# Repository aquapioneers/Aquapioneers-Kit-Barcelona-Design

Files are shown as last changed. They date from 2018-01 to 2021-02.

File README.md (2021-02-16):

# The Aquapioneers Kit Barcelona Design

The Aquapioneers kit can transform a 54L (60x30x30 cm) aquarium into an aquaponic ecosystem. At the intersection of hardware and ecology, the ecosystem will allow you to grow fresh and tasty food all year round. This little piece of nature, will engage and inspire you, your family and your friends.

What makes the Aquapioneers kit different from other aquaponics kits, is its open source design, which was designed so that anyone can download and manufacture the kit locally in any digital manufacturing workshop, maker space or fab lab.

aquapioneers kit

## CNC milling design files

- Version 1 for a 50L Aquarium could be download [here](https://github.com/aquapioneers/Aquapioneers-Kit-Barcelona-Design/tree/master/CAD%20Files/Version%201%20for%2050L%20Aquarium) 
- Version 2 for a 50L Aquarium could be download [here](https://github.com/aquapioneers/Aquapioneers-Kit-Barcelona-Design/tree/master/CAD%20Files/Version%202%20for%2050%20L%20Aquarium) 
- Version 2 for a 180L Aquarium could be download [here](https://github.com/aquapioneers/Aquapioneers-Kit-Barcelona-Design/tree/master/CAD%20Files/Version%202%20for%20180%20L%20Aquarium) 

## Aquapioneers Ecosystem anatomy

anatomy 1

## Project main documentation

The user manual has been divided into four blocks following the Aquapioneers Ecosystem anatomy to ease its construction, assembly and use.

anatomy 2

The release of this documentation is progressive, meaning that the so far “The Body”, "The Blood", "The Nervous System" and "The Life" parts have been published. These editions will be regularly updated as a whole to reflect the comments and questions of our community. 

## Video tutorials

aquapioneers kit

Last but not the least, we have created a [Youtube channel ](https://www.youtube.com/playlist?list=PLUFhb7gQAOXpYl2u4EjiyPYbu-uKQxlLc) where we post some video tutorials to help you out related to the FAQs when it comes to maintain the ecosystem

## Contributions & Community forum

We are constantly working on improving the documentation but still we encourage you to Fork the project and do a Pull request with your contributions. We thus encourage you warmly to leave any comments / suggestions / questions on our [forum](http://aquapioneers.io/community-forum/) to be part of our community-based continuous improvement!

## Open Source Non Commercial License - Why ?

All the hardware design files is released under creative license [CC-BY-NC 4.0](https://creativecommons.org/licenses/by-nc/4.0/).Thi  license gives anyone the right to download, edit and remix their own versions of the AQUAPIONEERS ECOSYSTEM designs. We think participation in design is something to be actively encouraged. By adapting, improving and creating new variations of the ecosystem we hope to encourage research, innovation and a spirit of collaboration.

Because empowering people is one of the fundamental pillars of our project, we believe that everybody should have free access to this documentation to explore aquaponics and digital fabrication. Unfortunately in 2017 it is not yet possible to make a living out of free work.. this is why we have decided to limit the free use of our work to individuals. While we hope to inspire sustainable innovation with our work, we believe that economic value created from inventions should also benefit the inventors. This is why commercial use of this documentation will only be permitted through formal collaboration agreements. If you are interested in making commercial use of this work, please get in touch with us at info@aquapioneers.io and we’ll do our best to find a way to work together!

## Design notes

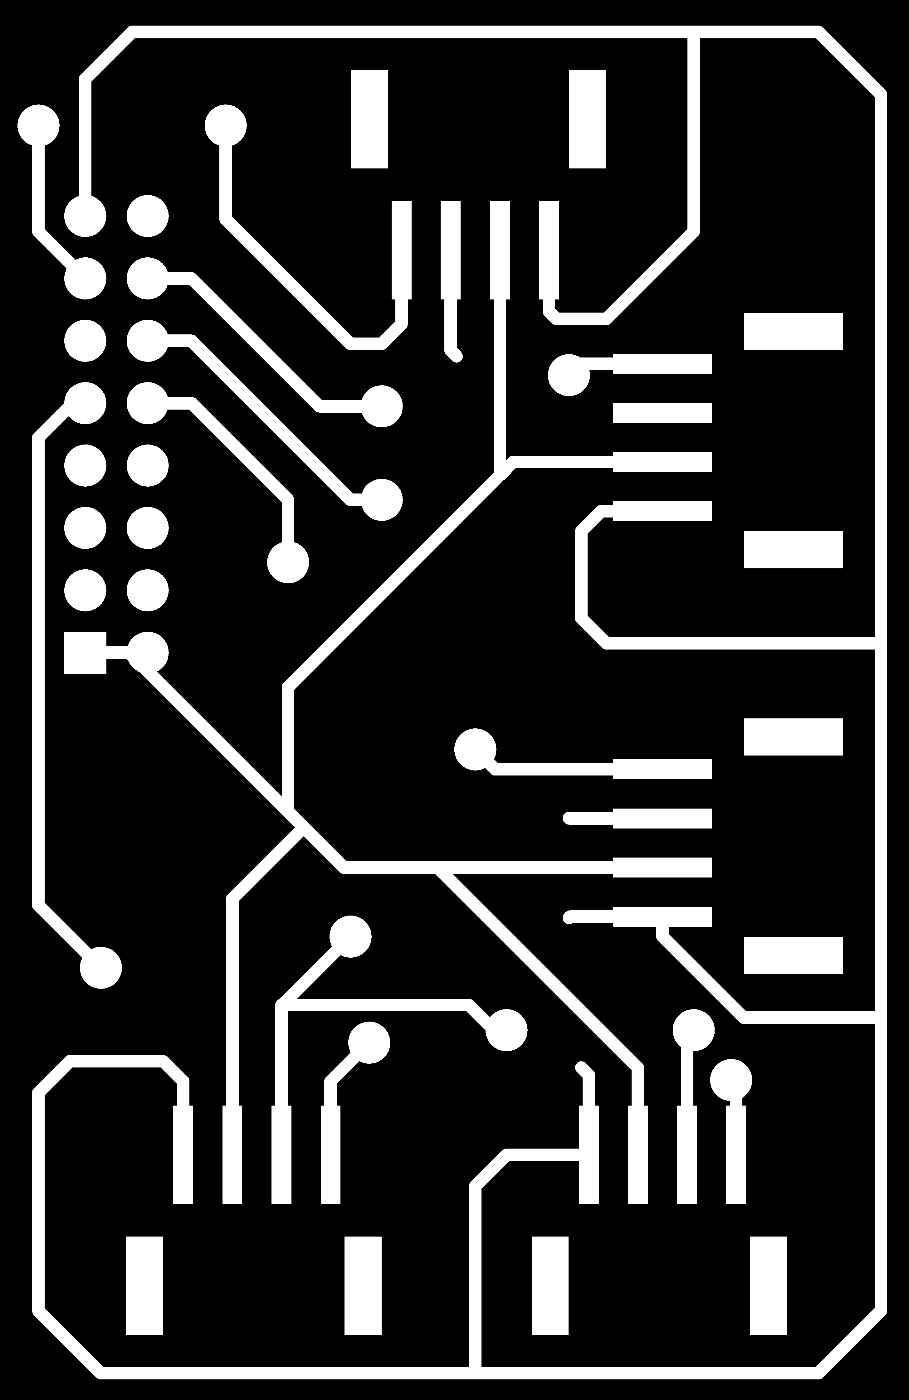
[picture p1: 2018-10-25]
Monitoring-kit-hardware/PCB layout/Aquapioneers PCB -Traces - Front.Cu.png

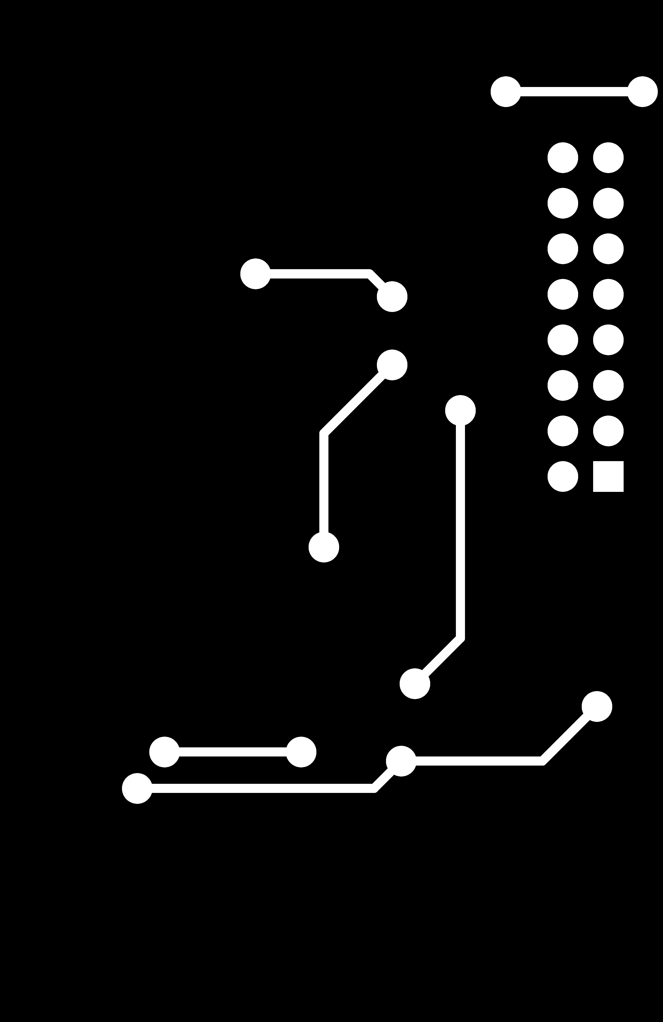
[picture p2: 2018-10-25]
Monitoring-kit-hardware/PCB layout/Aquapioneers PCB -Traces - Back.Cu.png

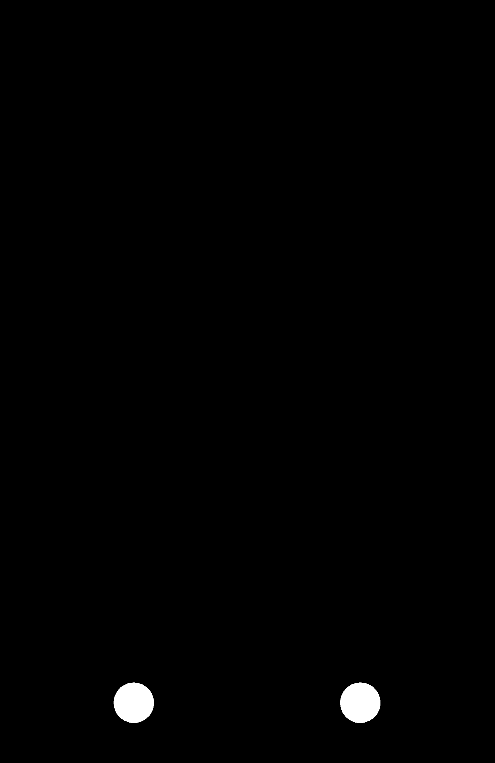
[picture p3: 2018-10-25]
Monitoring-kit-hardware/PCB layout/Aquapioneers PCB -Pins - Front.Cu.png

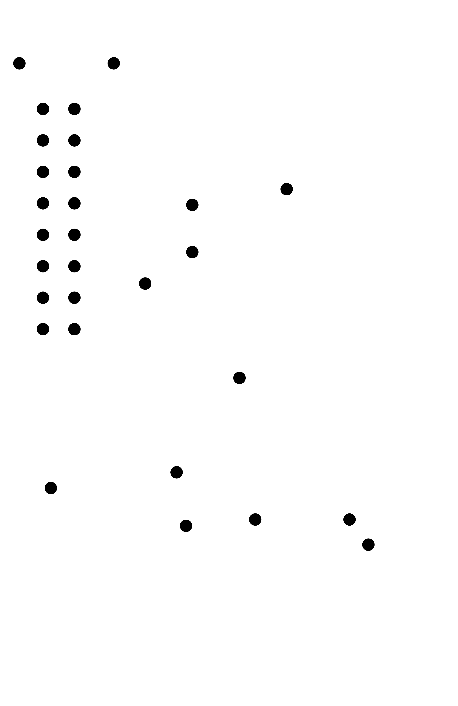
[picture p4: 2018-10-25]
Monitoring-kit-hardware/PCB layout/Aquapioneers PCB - Edge Cuts - Front.Cu.png

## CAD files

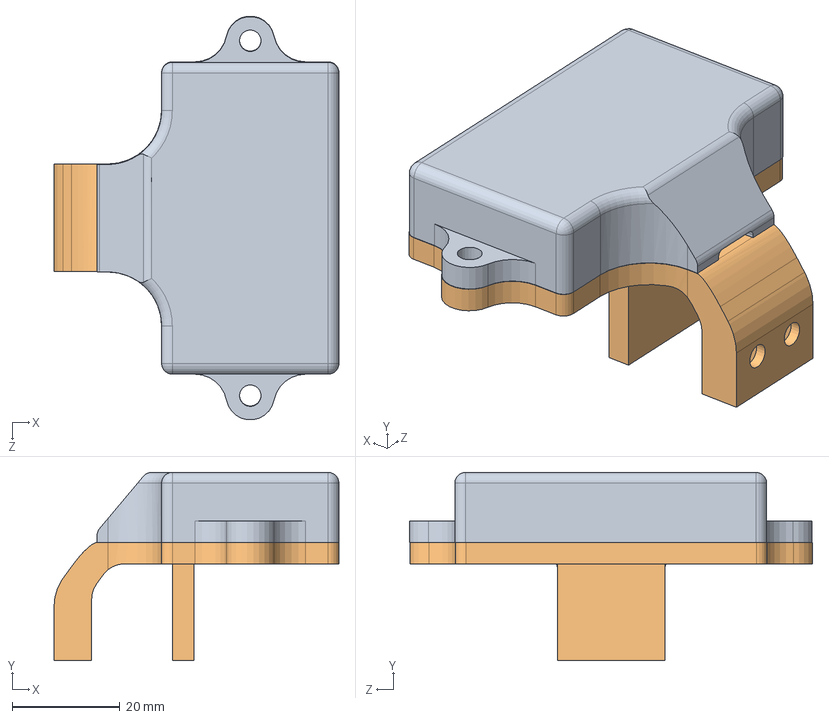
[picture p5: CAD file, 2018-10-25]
Monitoring-kit-hardware/3D printed ultrasonic sensor case/Assembly.SLDASM
53.0 x 35.0 x 75.0 mm
Top
Bottom
Ultrasonic_Ranger grove

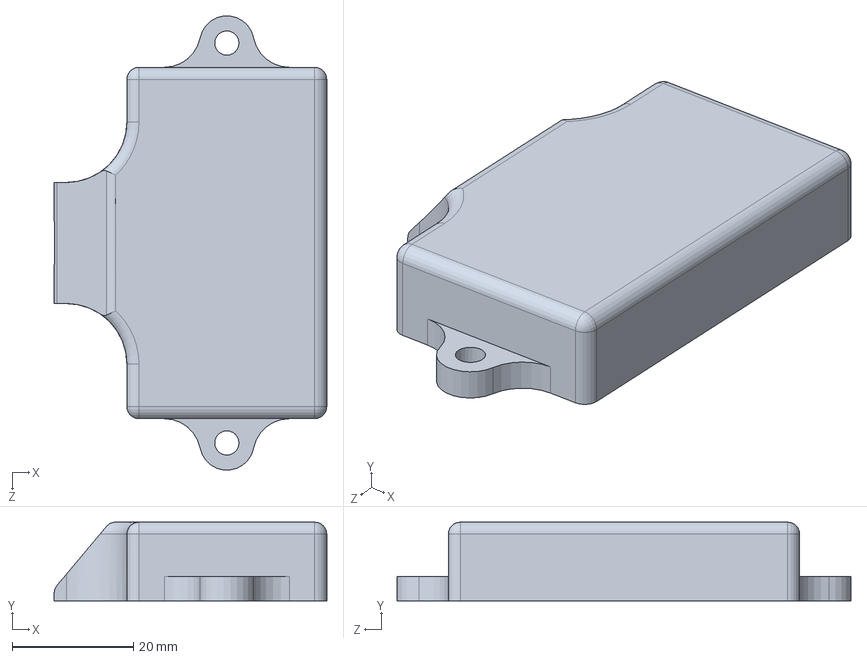
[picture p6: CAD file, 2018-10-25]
Monitoring-kit-hardware/3D printed ultrasonic sensor case/Top.SLDPRT
45.0 x 13.0 x 74.9 mm

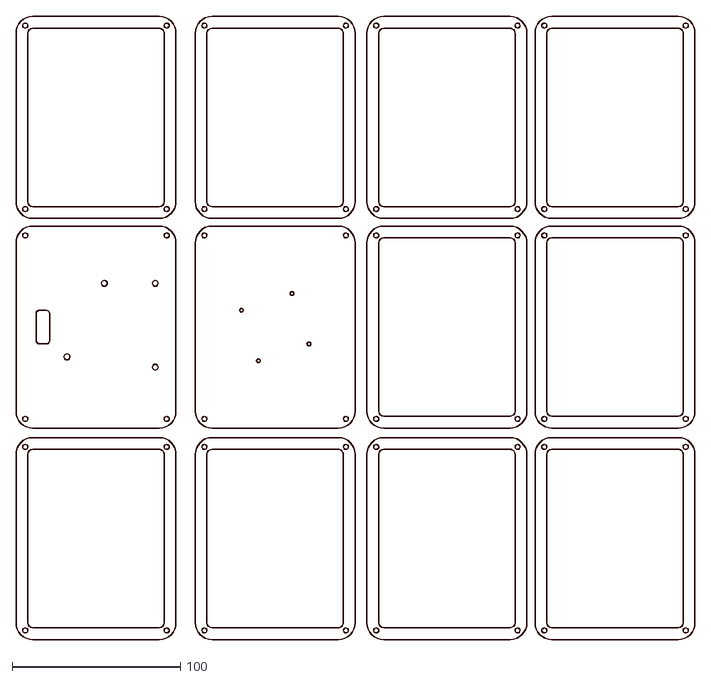
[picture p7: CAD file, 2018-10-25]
Monitoring-kit-hardware/Board case/Nesting Board Case.dxf
403.3 x 370.2

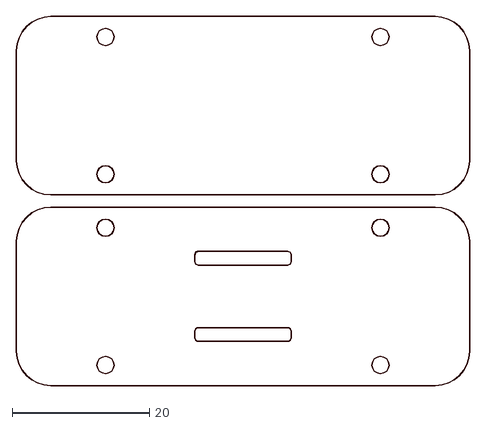
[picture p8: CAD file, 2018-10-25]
Monitoring-kit-hardware/SHT-31 and Light sensor/Nesting SHT-31 and Light sensor.DXF
66.0 x 53.8

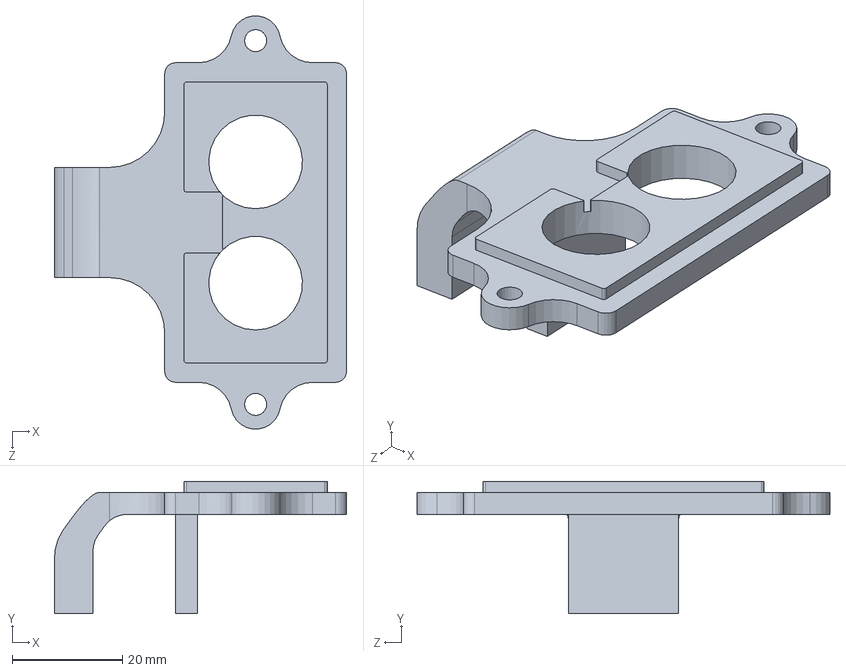
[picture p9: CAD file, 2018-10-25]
Monitoring-kit-hardware/3D printed ultrasonic sensor case/Bottom.SLDPRT
53.0 x 24.0 x 74.9 mm

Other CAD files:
CAD Files/Version 1 for 50L Aquarium/Aquapioneers_Kit_v1.6_18mm_Nesting-2.dwg
CAD Files/Version 2 for 180 L Aquarium/Aquapioneers_Kit_v2_18mm_180L_Nesting.DWG
CAD Files/Version 2 for 50 L Aquarium/Aquapioneers_Kit_v2_18mm_Nesting.dwg
CAD Files/Version 2 for 50 L Aquarium/Aquapioneers_Kit_v2_18mm_3D.dwg
CAD Files/Version 1 for 50L Aquarium/Aquapioneers_Kit_v1.6_18mm_Nesting-2.3dm
CAD Files/Version 2 for 180 L Aquarium/Aquapioneers_Kit_v2_18mm_180L_Nesting.3dm
CAD Files/Version 2 for 50 L Aquarium/Aquapioneers_Kit_v2_18mm_Nesting.3dm
Monitoring-kit-hardware/3D printed ultrasonic sensor case/Bottom.STL
Monitoring-kit-hardware/3D printed ultrasonic sensor case/Top.STL
Monitoring-kit-hardware/Board case/Rhino Nesting Board Case.3dm
Monitoring-kit-hardware/SHT-31 and Light sensor/Nesting SHT-31 and Light sensor.3dm

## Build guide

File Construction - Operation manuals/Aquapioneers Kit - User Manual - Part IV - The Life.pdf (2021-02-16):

# Download kit

### Free documentation & blueprints for Aquapioneers Kit Part IV - Biological System - The Life

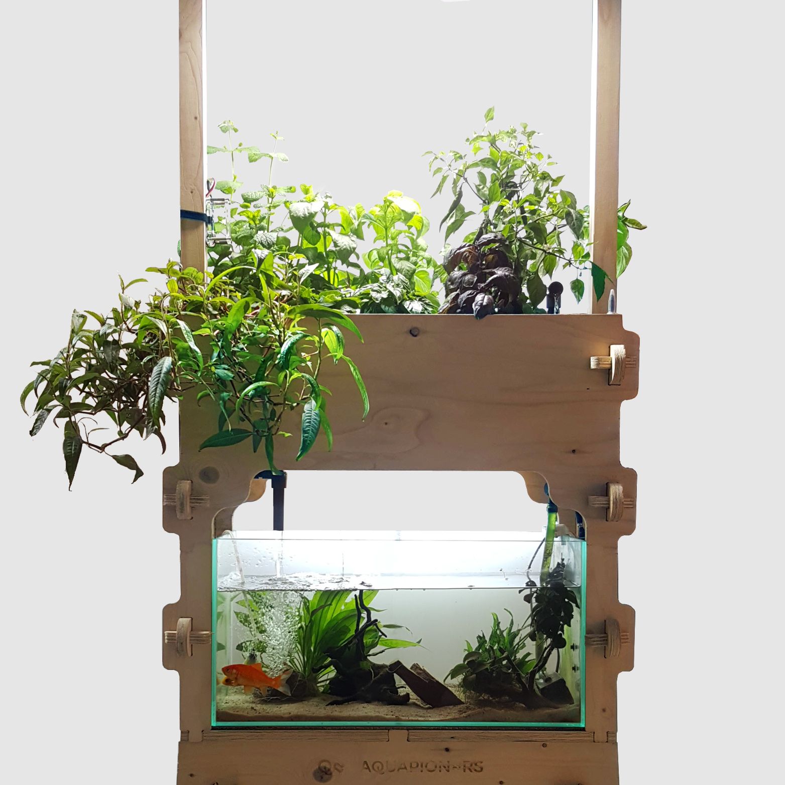
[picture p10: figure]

1. Almost ready to have your fresh aromatics all year round ! | 3
2. Starting up (cycling) your ecosystem | 4
2.1 Bill of materials | 4
2.2 Start the water irrigation system | 5
2.3 Start cycling your ecosystem | 8
3. Troubleshooting | 10
3.1 The bell siphon | 10
3.2 The water inlet | 12
4. Some species of fish that can inhabit your ecosystem | 15
5. Some herbs and leafy greens you can grow | 15
6. How to care for your kit | 16
6.1 Daily tasks | 16
6.2 Weekly tasks | 18
6.3 Ranges for water quality parameters | 21
Annex I : Aquaponic design ratios | 23
Annex II: Interesting Aquaponics links | 24

# 1. Almost ready to have your fresh aromatics all year round !

In less than two months, your Aquapioneers Kit could look likes something like the picture below. However there are some crucials biological steps to put in place before your aquaponics jungle takes place. In this section we will explain you how to kickstart the biological ecosystem and how to take car of it in order to grow with confidence.

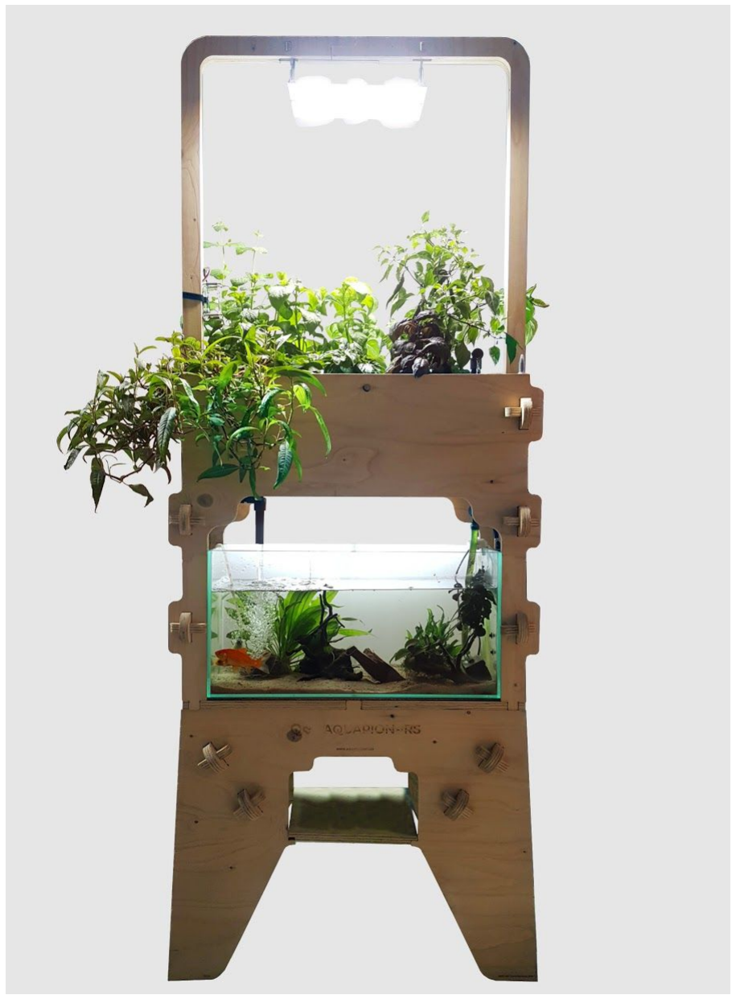
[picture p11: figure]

# 2. Starting up (cycling) your ecosystem

An aquaponic system needs about a month to establish a biological equilibrium between plants, fish and bacteria. This is due to the fact that the bacteria which filter the fish waste grow very slowly on the filter material we put at their disposal. While these nitrifying bacteria are ubiquitous and do not need to be artificially introduced into the system, it is fundamental to introduce a source of ammonia (NH4), simulating fish waste, which they can “train” to decompose into the nitrate (NO3) fertilizer we are after. We should not introduce fish until the filter is properly established, since these might die by self-intoxication. The safest way to do this is to add controlled dosages of ammonium chloride, a cheap and harmless chemical available. Nitrite concentrations should be monitored. Over time, ammonia (NH4) will be degraded first into nitrite (NO2) and finally into nitrate (NO3), so that globally, if you measure all three components over time, you should get a graph similar to the something below:

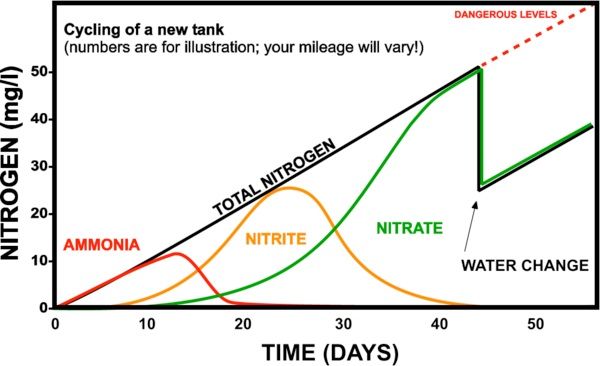
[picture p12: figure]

## 2.1 Bill of materials

For this you will need the following:

35 L of PH 7
clay pebble

Ammonium chloride
(AC) powder

NH4
water test

NO3
water test

NO2
water test
Price: 10-15€ | Price: 1€ | Price: 10€ | Price: 10€ | Price: 10€

## 2.2 Start the water irrigation system

1

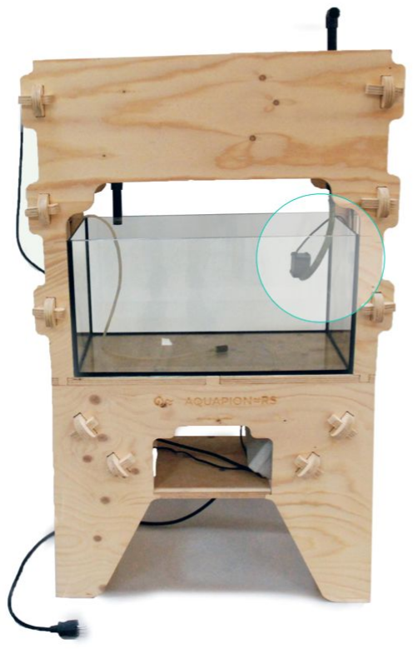
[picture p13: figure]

The entire electrical system is now in place, but “Do not plug your system to the mains power” until there is water in the fish tank, as this will run your water pump dry and possibly destroy it. To facilitate adding water to the aquarium you will remove the growbed for a while. To do so, first disconnect the flexible pipe to the water pump connector and the 12 Volts LED strip connector as well.
2

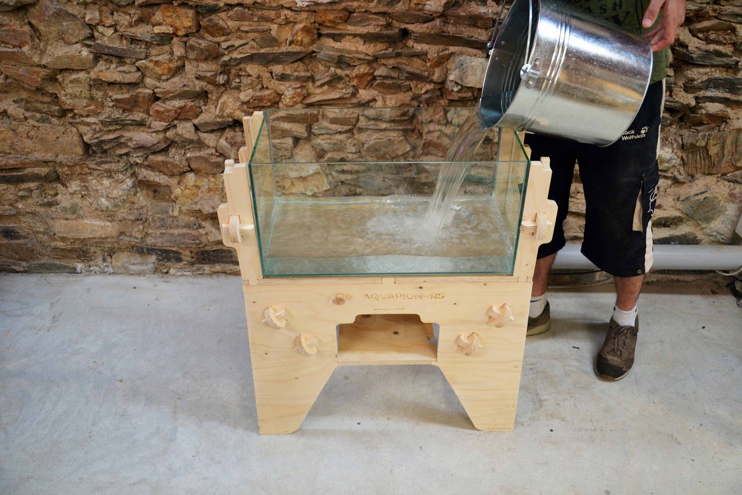
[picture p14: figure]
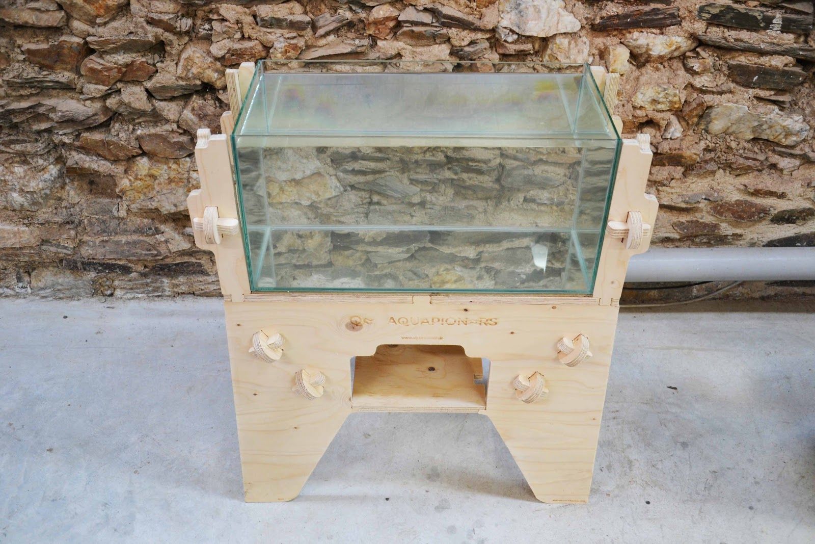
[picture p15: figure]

You will be able then to fill the aquarium. Tap water is OK.

3

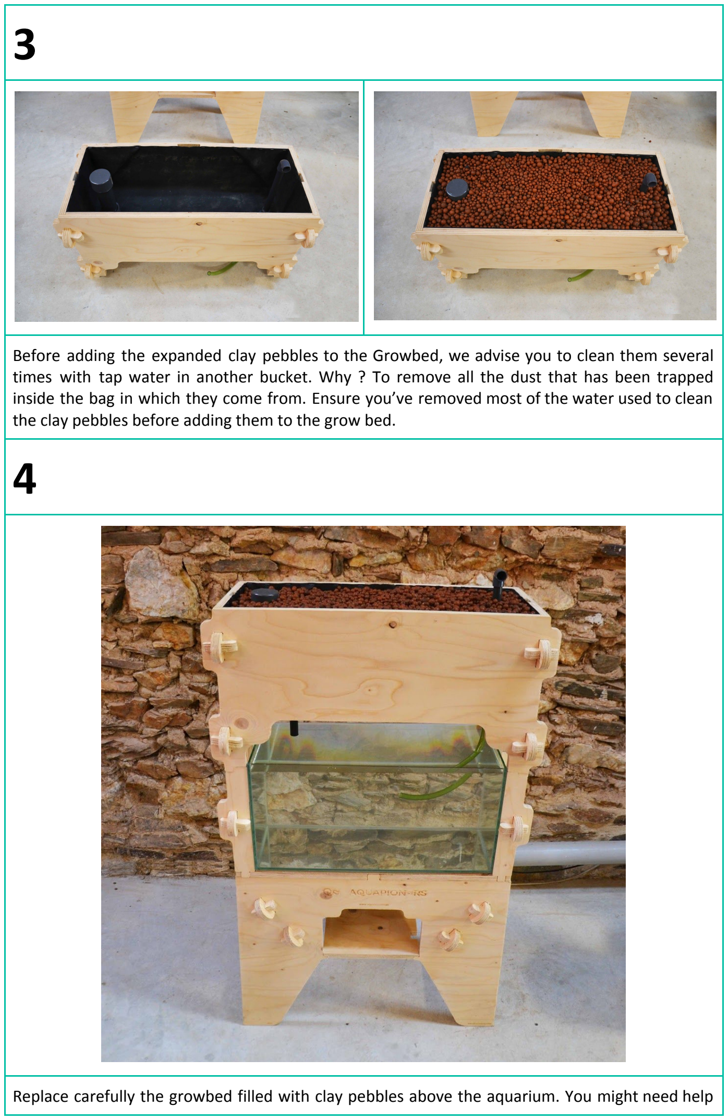
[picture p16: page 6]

Before adding the expanded clay pebbles to the Growbed, we advise you to clean them several times with tap water in another bucket. Why ? To remove all the dust that has been trapped inside the bag in which they come from. Ensure you’ve removed most of the water used to clean the clay pebbles before adding them to the grow bed.
4

Replace carefully the growbed filled with clay pebbles above the aquarium. You might need help from a peer since it could be quite heavy.
5

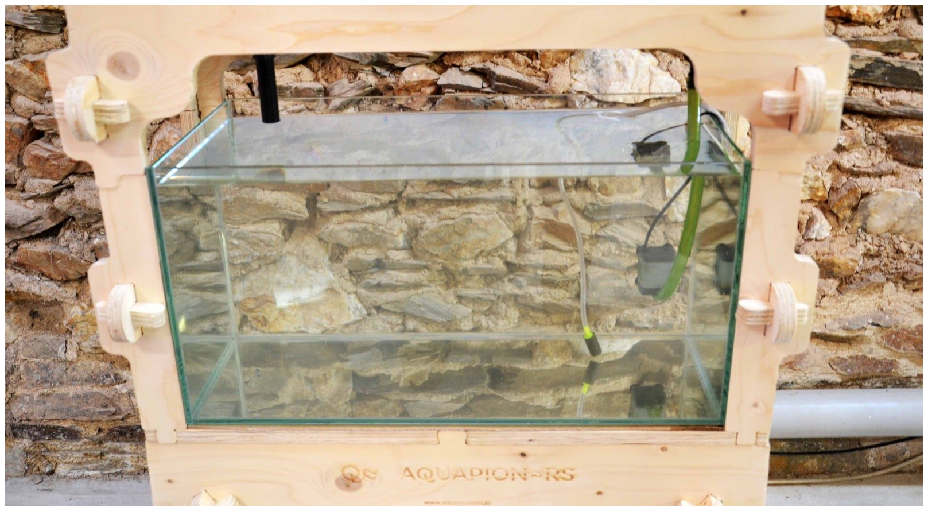
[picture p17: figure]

Replace the water pump inside the aquarium by reconnecting it to the green flexible pipe. Add the air pump tube in the aquarium as well.
6

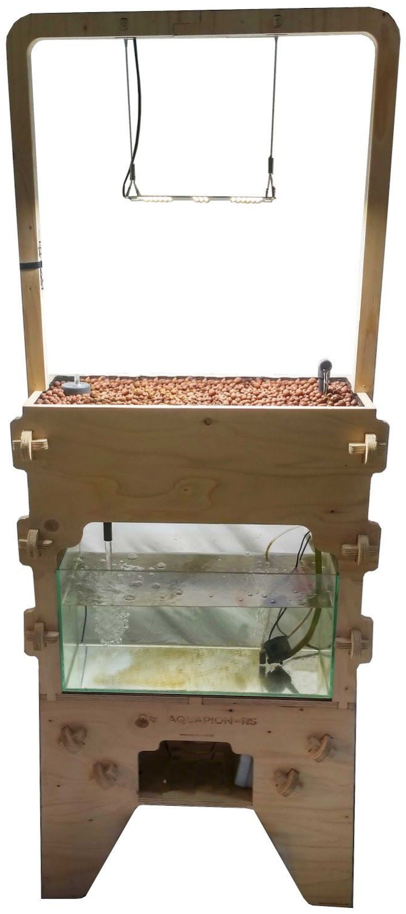
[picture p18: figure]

Last but no the least, you can add the lighting structure on top of growbed. However, please note that till your ecosystem is not cycled and planted you will not need to use the growing light. Before connecting your system to the main power, just make sure your electrical box is sealed. Then here you go !

## 2.3 Start cycling your ecosystem

1

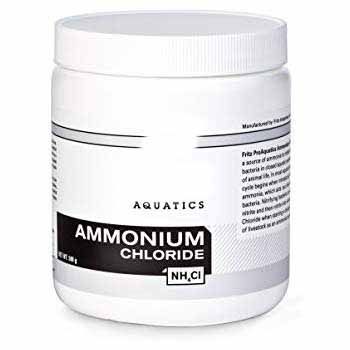
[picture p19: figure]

With an Aquapioneers kit of 50 L, we recommend to introduce ammonium chloride (AC) powder and test for ammonia, nitrite and nitrate with the help of the table on the following page (we recommend to print it and put it next to the kit to ease the follow up). An “X” marks the days in which we recommend to carry out the corresponding water test. The number in the column “AC dosis (g)” corresponds to the amount of ammonium chloride chemical to introduce into your system on that day. This dosage increases over time as the bacteria community grows stronger and is able to process more waste, until it matches the amount of ammonia produced daily by the amount of fish we’d like to introduce into our system.
2

IMPORTANT: If you want to use this table on a system with different size and amount of fish, you will need to adapt the dosages you introduce to your system. Do do this, IF you follow the design principles in Annex II, just divide the number in column 3 by 50, and then multiply by the amount of liters in your system. For example, if your system has 600 liters as in the example in section 2, the first dosis of ammonium chloride you need to introduce will be 0.2 g / 50 liters * 600 liters = 2.4 grams of ammonium chloride (AC).

Notes:
- The test should be carried out before introducing a new ammonium chloride dosis.
- The kit is properly cycled (and safe for fish) once nitrite (NO2) levels remain below 0,15 mg / Lt after minimum 2 weeks of cycling.

## Guide to start the nitrogen cycle for the Aquapioneers kit

Day | Date | AC dosis (g) | NO2 test | Value | NO3 test | Value
1 | | 0.2 | X | | X

2

3

4

5

6

7 | | 0.2 | X | | X

8

9

10

11 | | 0.2 | X | | X

12

13

14

15

16

17

18 | | 0.4 | X | | X

19

20

21

22

23

24 | | 0.6 | X | | X

25

26

27

28

29

30 | | 0.8 | X | | X

31

32

33 | | 0.8

34

35

36 | | 1.2 | X | | X

37

38

39 | | 1.2

40

41 | | | X | | X

# 3. Troubleshooting

Once your system is running, you might “or not” encounter some mechanical or electrical issues. You will find the most common ones below with our troubleshooting approach.

## 3.1 The bell siphon

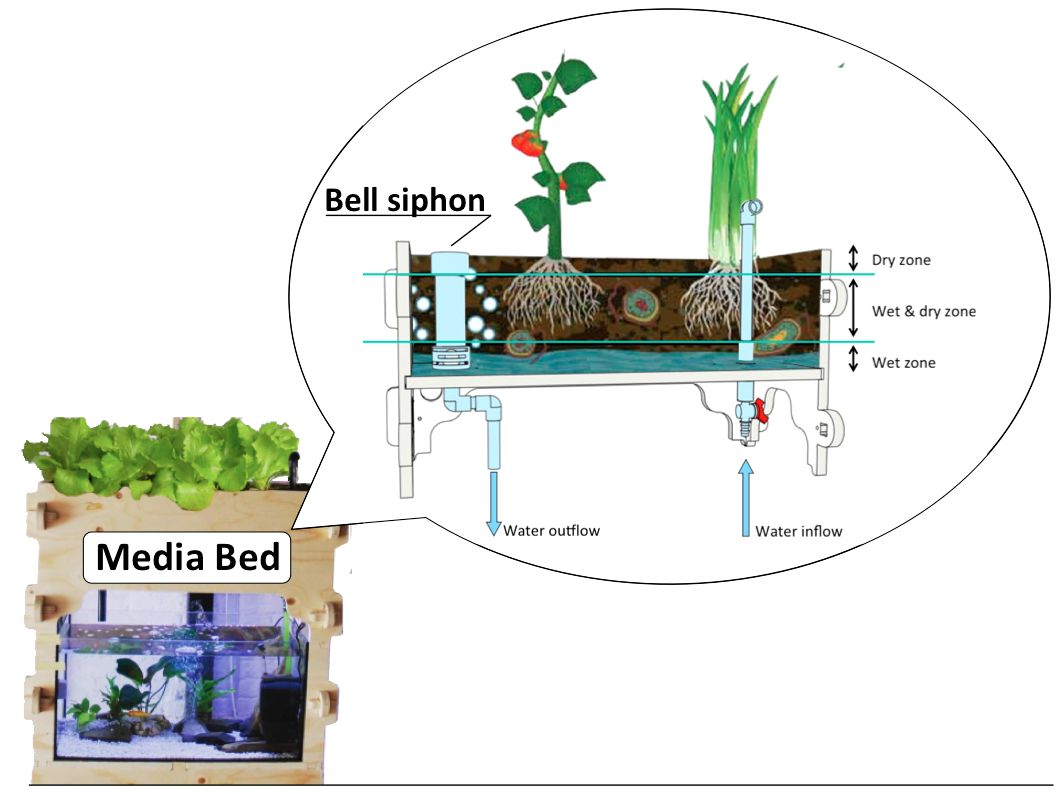
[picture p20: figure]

Media Bed technique that is used in the Aquapioneers kit, works with a Bell siphon which is a type of autosiphon that exploits a few physical laws of hydrodynamics and allows the media bed to flood and drain automatically, periodically, without a timer. This alternation ensures both high humidity and high oxygen levels in the Media Bed - exactly what your plant roots and nitrifying bacteria need! There is one downside to the bell siphon: Its proper function depends on the water flow of your pump. A correctly operating bell siphon drains the entire media bed water in less than a minute, then completely stops flowing until the media bed is full of water again, and the cycle starts anew.

If the water flow from the siphon is low (+/- the flow of the water inlet) and the water level remains constant, your Bell Siphon is not working correctly. If left unattended, in a matter of days this could mean the death of your fish. If you are not sure whether your bell siphon is working or not, test your nitrite (NO2): After a day of malfunction, you will detect a nitrite increase in your system. If this is your case:

TROUBLESHOOTING 1: Your media Bed stays full

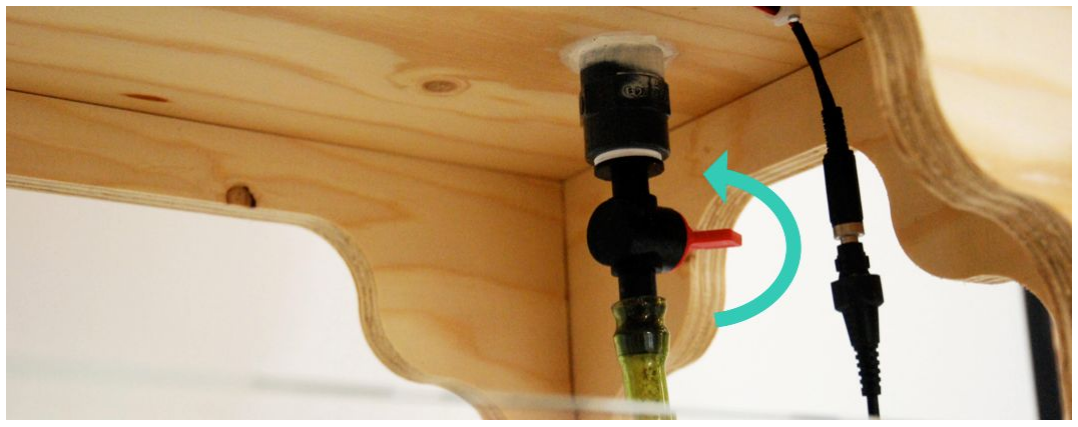
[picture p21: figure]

The water flow is too low. Use the valve to slightly increase the water flow. Wait a few minutes. If the problem persists, do this again. Repeat the process until the problem is fixed. Note: The siphon is very sensitive to the flow rate, only turn the valve as little as possible in order to avoid your flow becoming too high.

TROUBLESHOOTING 2 : Your media Bed stays empty

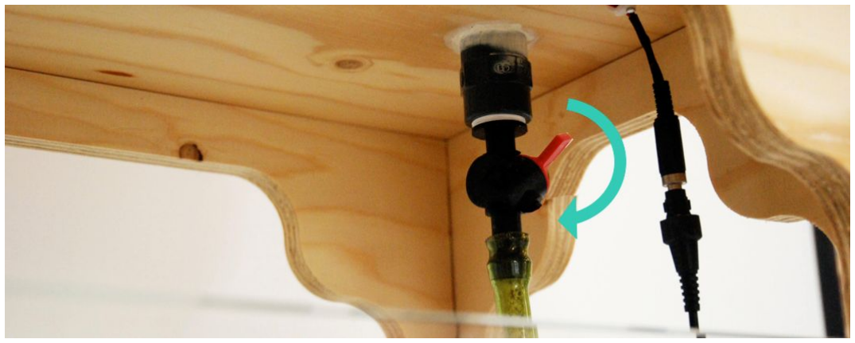
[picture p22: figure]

The water flow is too high. Use the valve to slightly reduce the water flow. Wait a few minutes. If the problem persists, do this again. Repeat the process until the problem is fixed. Note: The

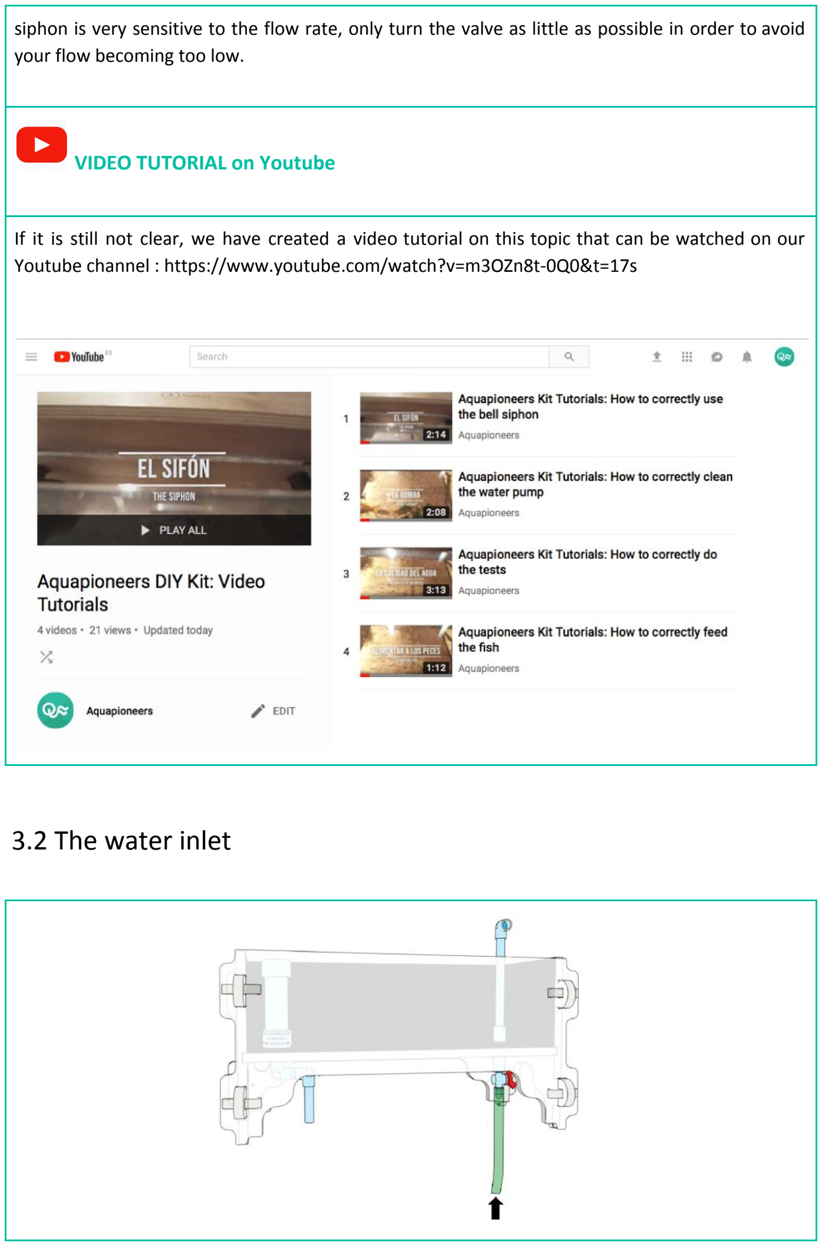
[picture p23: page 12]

siphon is very sensitive to the flow rate, only turn the valve as little as possible in order to avoid your flow becoming too low.

VIDEO TUTORIAL on Youtube

If it is still not clear, we have created a video tutorial on this topic that can be watched on our Youtube channel : https://www.youtube.com/watch?v=m3OZn8t-0Q0&t=17s

## 3.2 The water inlet

The water inlet on top of your media bed delivers the aquarium water to the plants. The inlet is connected to the pump which is located at the bottom of the aquarium, via the transparent tube. A valve below the Media Bed regulates the flow of the water inlet. As the pump is simply connected to electricity, it should run whenever your kit is plugged in. Therefore the water inlet should supply water continuously. If no water is coming out of the inlet, follow the following steps to troubleshoot the issue. It is critical that the problem is resolved quickly, because a dry inlet means that your media bed is no longer filtering the fish water. If left unattended, your fish may die in a couple of days time!

TROUBLESHOOTING 1 : The electrical system is failing

In the event of an electrical failure, your pump will evidently stop working. You will easily identify this case since all your electrical components will stop working, such as the grow light and the air pump. If your other elements are working, move on to point 2) If all your electrical components are failing, walk through the following steps:

- Make sure the kit is connected to the power supply.
- Make sure your power supply has not been affected.
- If you have determined your electrical supply is working but not your kit, there might be an issue in the electrical system of your kit. We strongly encourage calling an electrician to resolve the problem. If you decide to debug it yourself, make sure to disconnect your kit from the power socket before you do!

TROUBLESHOOTING 2 : Your valve was closed by mistake

The valve controlling your inlet flow might be on the “closed” position. If it is the case, open it back to the position that enables the bell siphon to function correctly (see section on the bell siphon). Try to see if the valve is closed without touching it, because if you do, you might have to readjust the water flow (--> see section 2.1 ).

TROUBLESHOOTING 3 : Your pump is obstructed

The pump delivering the water to your plants might have been obstructed. This may occur if :
- Your pump inlet has been blocked by algae and bacteria. You can easily avoid this situation by cleaning your pump once a month.
- Debris from the aquarium has blocked the inlet.
- Debris from the aquarium is blocking the rotor inside the pump. THIS IS ESPECIALLY LIKELY TO OCCUR IF YOU USE COARSE SAND (~2-3 mm diameter) AS AQUARIUM DECORATION. Individual particles tend to enter the pump and block the rotors motion. Avoid this type of decoration.

To resolve this issue, unplug your kit from electricity, then disconnect the pump from the transparent tubing in order to clean it.

Water pumps break if left to run dry = if air enters the pump. Never remove your pump from the water without disconnecting electricity! This would damage it irreparably.

Most pumps are easy to take apart for cleaning. Before you set up your system, make sure you know how to open your pump until the rotor comes out (the inner piece with blades which rotates)! Take it apart in the water and use a small brush to clean the parts. Remove any debris (or sand particles) and make sure the rotor can freely rotate before putting the pump back together. Once reassembled, put the pump back into the water. Connect the pump back to the transparent tubing and plug back the electricity. You should be good to go!

VIDEO TUTORIAL on Youtube

If it is still not clear, we have created a video tutorial on this topic that can be watched on our Youtube channel : https://www.youtube.com/watch?v=pN3SSN_O0qc&t=4s

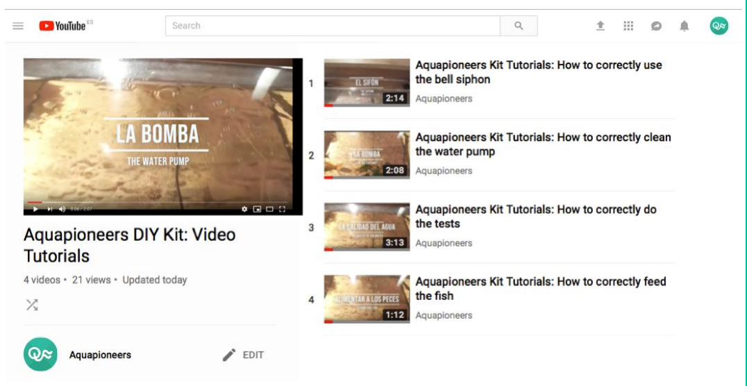
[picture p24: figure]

# 4. Some species of fish that can inhabit your ecosystem

Congratulations on setting up your brand new Aquapioneers kit! Now starts the exiting time, introducing our lovely fish ! But the big question is which one ? and how many could live in a 50L aquarium respecting their well being. Below are just a few examples of freshwater fish available in almost every aquarium stores around the world. However, for the ones that don’t have any previous experience with aquariums, we recommend to start with Goldfish !

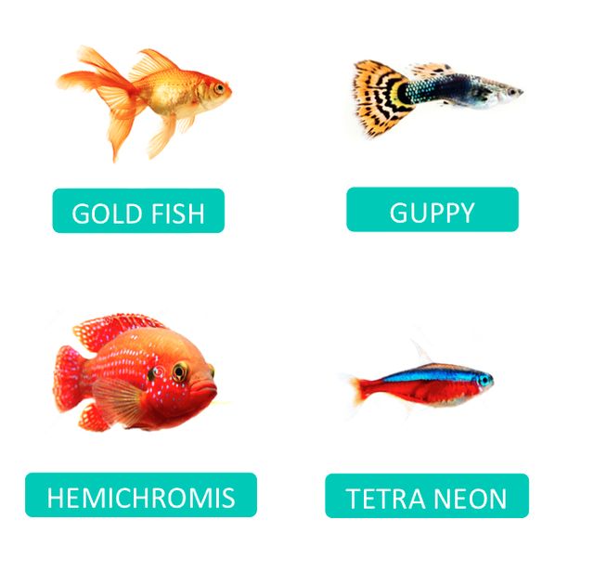
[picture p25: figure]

VIDEO TUTORIAL on Youtube

When it comes to feed them, we have created a video tutorial to guide you on our Youtube channel : https://www.youtube.com/watch?v=it17Tjr0Hbc

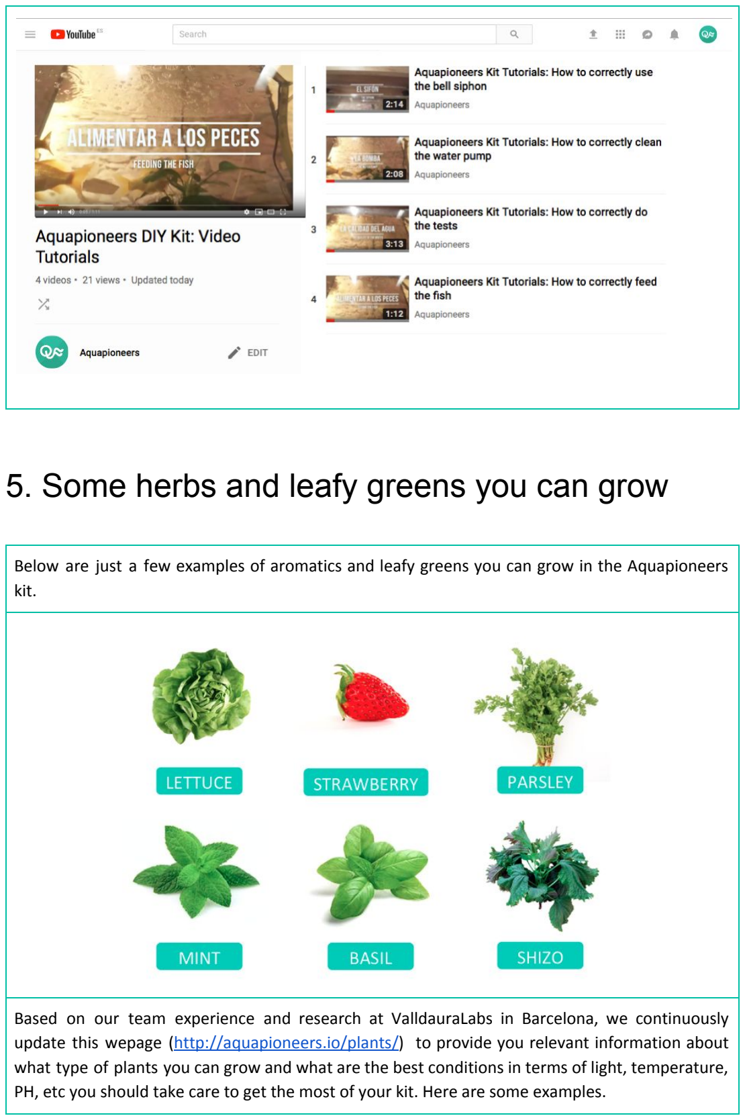
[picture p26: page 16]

# 5. Some herbs and leafy greens you can grow

Below are just a few examples of aromatics and leafy greens you can grow in the Aquapioneers kit.

Based on our team experience and research at ValldauraLabs in Barcelona, we continuously update this wepage (http://aquapioneers.io/plants/) to provide you relevant information about what type of plants you can grow and what are the best conditions in terms of light, temperature, PH, etc you should take care to get the most of your kit. Here are some examples.

# 6. How to care for your kit

Congratulations on setting up your brand new Aquapioneers kit! In order to make sure your fish and plants grow healthy there are a few simple steps you need to regularly follow. While these tasks are quite simple, it is essential that you follow them as instructed, and when instructed, without which you could end up terribly frustrated.

## 6.1 Daily tasks

Probably the most important Keep an eye open on a daily basis. Ecosystems can be fragile, and sooner or later problems may arise. Most problems can be avoided by detecting the signs early.

As you get to know your ecosystem, the signs will become obvious to you. What you should be looking out for:

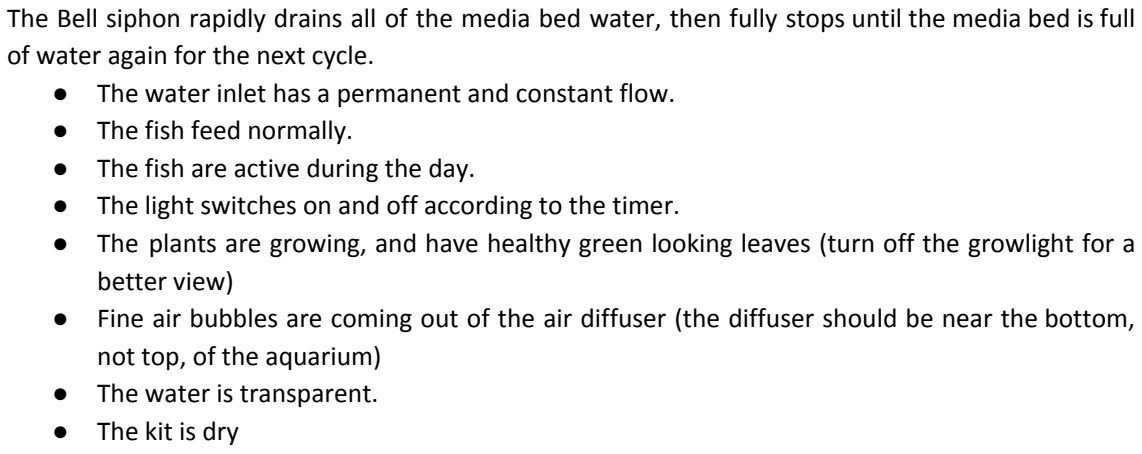
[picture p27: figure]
of water again for the next cycle.; ● The fish feed normally. ● The fish are active during the day.; better view); not top, of the aquarium) ● The water is transparent. ● The kit is dry

The Bell siphon rapidly drains all of the media bed water, then fully stops until the media bed is full

- The water inlet has a permanent and constant flow.
- The light switches on and off according to the timer.
- The plants are growing, and have healthy green looking leaves (turn off the growlight for a
- Fine air bubbles are coming out of the air diffuser (the diffuser should be near the bottom,

To ease this daily follow up, we’ve prepared a printed version (following page) that can be added next to your kit

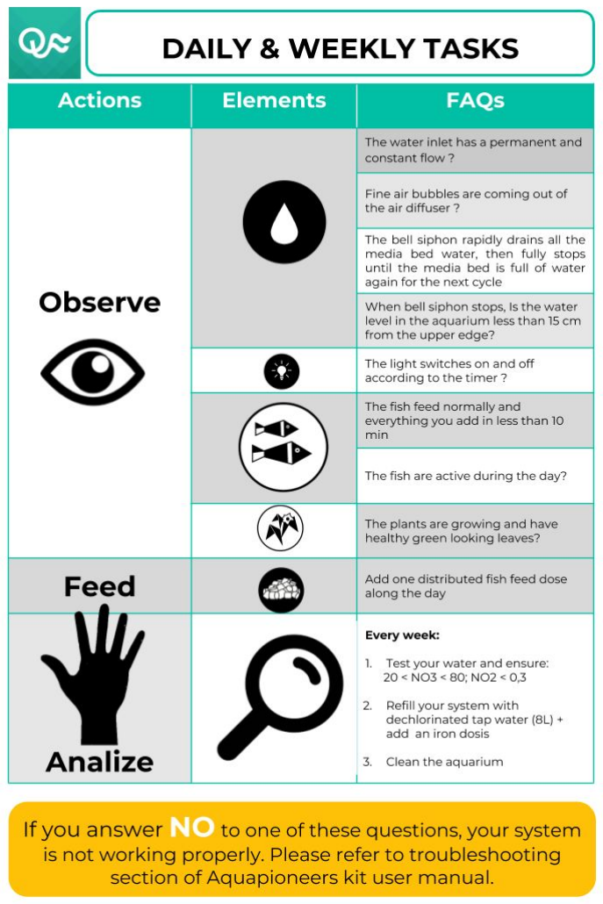
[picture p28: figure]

## 6.2 Weekly tasks

Choose a day of the week to do your basic maintenance tasks to make sure you are regular in your care. Let’s assume this day is saturday. Every saturday you will need to:

REFILL YOUR SYSTEM WITH DECHLORINATED WATER : to compensate for the water used by your plants

- Put around 8 L tap water in a container.
- Dechlorinate the water. In most countries tapwater contains chlorine which needs to be removed because it is toxic for the fish. You have 2 options:
- If you want to be able to use it instantly, purchase a dechlorinating product from your nearest fishkeeping store. Dose it according to manufacturers instructions and mix it with the water you prepared.
- Leaving the water in a bucket for 24h will let the chlorine evaporate and make your water safe to use without using chemicals!

ADD IRON TO THE WATER FOR HEALTHIER PLANTS

In aquaponics, iron tends to be deficient. It can be added under the form of an iron chelate (we highly recommend the EDDHA type, make sure you get one that does not significantly colour your water at recommended dosages!) :
- Weigh out 0.4 g of iron chelate and dissolve it in the water you dechlorinated,
- OR
- You can purchase vials that were carefully weighed by our team. You just empty the vial into the water, and you're done.

VIDEO TUTORIAL on Youtube

If it is still not clear, we have created a video tutorial on these two topic that can be watched on our Youtube channel : https://youtu.be/BWA90jbF0Qo

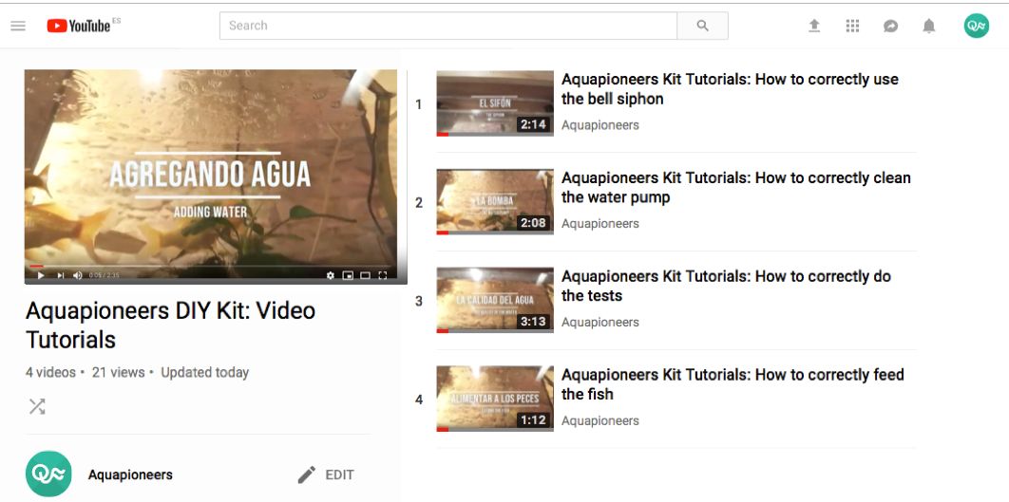
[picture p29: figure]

CLEAN THE AQUARIUM

To keep your system beautiful and shiny, and avoid algae growth, you should clean your aquarium every week. We recommend to use magnetic sponges made for that purpose, which allow you to clean the tank easily and without getting wet!

TEST YOUR NITRITE AND NITRATE CONCENTRATION

This should be done twice a week, or every time you suspect your bell siphon / filter might not be working correctly. You may reduce testing frequency once you have become accustomed to your system and know how to detect the reasons behind nitrite accumulations. Nitrite (NO2) is a toxic intermediate in the transformation of fish waste (ammonia NH4+) to plant fertilizer (Nitrate NO3). Test kits are available in every fishkeeping store. In a well functioning system ammonia and nitrite are kept at very low levels by the essential nitrification bacteria living in the Media Bed.

If your Nitrite concentration is above 0.1 mg/L, this is a sign that :
1. Your system has not finished the cycling process (see section "Setting up your aquaponics kit) and is NOT ready to host fish.
OR
2. Your filter (= the Media Bed) is not functioning correctly.

The most common reasons for high Nitrite concentrations are:
- The bell siphon is not working properly (see the "bell Siphon infografic")
- A drastic change occurred in your system. Significant changes in Temperature, pH, oxygen levels can damage both your fish and your nitrifying bacteria. Avoid shocking your system in any way.

VIDEO TUTORIAL on Youtube

If it is still not clear, we have created a video tutorial on these two topic that can be watched on our Youtube channel :https://www.youtube.com/watch?v=LoWL6dGzlHY

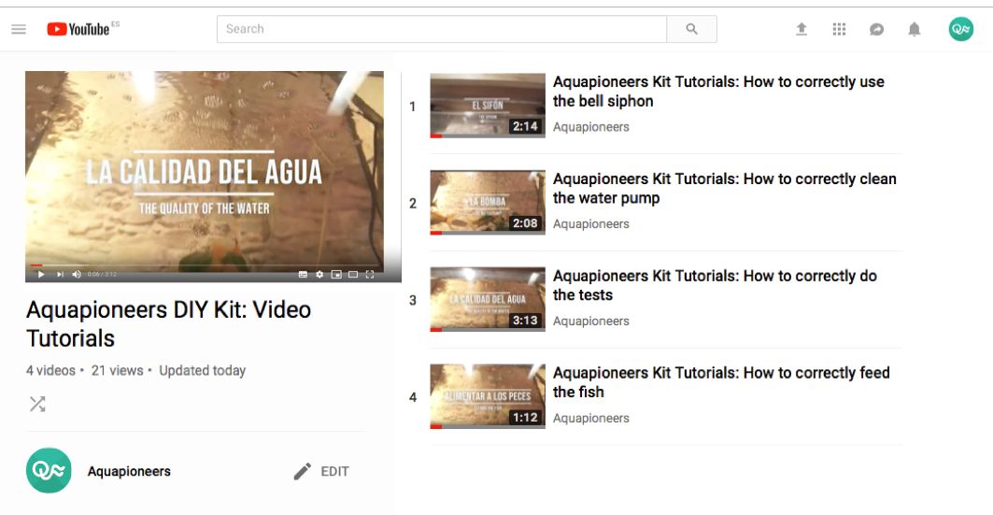
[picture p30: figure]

INSPECT YOUR PLANTS CLOSELY to detect any bugs or unusual colors on the leaves. The earlier you detect pests the easier they are to remove.

ATTENTION!! Since your kit is an ecosystem, it is strictly prohibited to use conventional insecticides on your plants!! They might kill your fish and / or the vital microorganisms in your system!

Soft alternatives must be used, do your research carefully before attacking bugs that might find their way to your kit!

The | team | of | Bright | Agrotech | did | a | great | job | with | their | blog
(https://blog.brightagrotech.com/pesticides-for-aquaponics/ ) and youtube videos (Pest Controls for Aquaponics - YouTube) on the subject!

# 6.3 Ranges for water quality parameters

For aquaponics to work properly and avoid danger to its organisms, water quality needs to be monitored and controlled to fit into the following recommended ranges:

Physical parameters | How to increase | How to decrease
pH | 6 < x < 8 | Add plants, remove fish, decrease feed, change water source, add pH affecting chemicals (can be dangerous, not recommended!) | Remove plants, add fish, increase feed, change water source,add pH lowering chemicals (can be dangerous, not recommended!)
EC (mS / cm) | 0.5 < x < 2 | Remove plants, add fish, increase feed, change water source, add fertilizers | Add plants, remove fish, decrease feed, change water source, dilute with more fresh water
Temperatura (deg C) | 16 < x < 28 | Add water heating, improve insulation | Add water cooling, improve insulation, add shading material
Dissolved oxygen DO (ppm) | 6 < x < 8.5 | Add air diffusers, add water cascades | Not required, there is never too much oxygen
Chemical parameters (mg / L or ppm) | | How to increase | How to decrease
NH4 | < 0.25 | Not required, should be as low as possible | Add plants, remove fish, decrease feed, add bacteria, add ammonia-removing substances
NO2 | < 0.5 | Not required, should be as low as possible | Fix filter issues, decrease feed, add bacteria, add nitrate-removing substances, remove fish
NO3 | 20 < x < 100 | Increase feed, remove plants, add fish, add N fertilizer | Decrease feed, add plants, remove fish
PO4 | 0.2 < x < 10 | Increase feed, remove plants, add fish, add P fertilizer | Decrease feed, add plants, remove fish
K | 6 < x < 30 | Increase feed, remove plants, add fish, change water source, add K fertilizer | Decrease feed, add plants, introduce fruiting plants (strawberries, tomatoes etc.) remove fish

Fe | 0.5 < x < 3

Add iron chelate (EDDHA type), mineralize solid fish waste

Reduce | iron
supplementation

Notes:

a) These values are recommended values based on our experience in Aquapioneers. We have worked mostly with relatively tolerant fish species (tilapia, guppy, goldfish, carps). If you consider trying with other fish species, it is essential that you check toxicity values for these fish which may be lower than the values given here.
b) pH, EC, Temperature, DO, NH4 and NO2 are essential to fish health, while NO3, PO4, K and Fe generally are relevant to plant health only (unless they reach extreme values not generally encountered).
c) pH and EC can be measured with inexpensive electronic meters, dissolved oxygen monitoring is expensive and not usually necessary at small scale if the tanks are well aerated, but is a must for professional applications. The most inexpensive means of monitoring chemical parameters is to use chemical testing kits available in fish stores, as we did in the workshop.

# Annex I : Aquaponic design ratios

An aquaponic system needs to be properly balanced between the 3 components: Fish, Plants & Bacteria. There have to be enough fish to generate the fertilizer needed by the plants, and there needs to be sufficient filtration (= Bacteria) to transform the produced fish waste into fertilizer. Steps:

a) Choose a given surface of plants
b) Calculate the amount of fish food needed (1 square meter of plants requires on average about 45 grams of fish food per day)
c) Calculate the filtration surface you need. For this, multiply the total daily amount of fish feed per day (in grams!) by 0.0657 to obtain the filtration surface you need to process the waste.
d) Calculate the volume of filter media you need. Many materials can be used as filtration media, and every media has a specific surface (how many meter squared of surface do I get for 1000 liters of material. For example, gardening Clay pebbles have about 250 m2 / 1000 liters of media. To obtain the volume of needed filter material in m3, divide the filtration surface you obtained in the previous step by the specific surface area (in this case, 250). To be safe, multiply this number by 1.5. Other examples of filtration materials, with their specific area, are given in the table below.

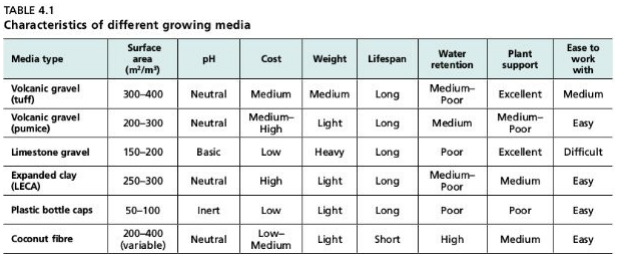
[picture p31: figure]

e) Calculate the total weight of fish you need to have in your system on average, knowing that generally fish in the growth stage feed on about 2 % of their bodyweight per day.
f) Calculate the size of your fish tank. In home systems, you should not exceed 20 kg of fish per cubic meter (1000 liter).

EXAMPLE

a) We’ll choose a total surface of 5 square meter plants.
b) We’ll need 5x 45 grams of feed per day = 225 grams per day.
c) Filtration surface needed = 225 grams per day x 0.0657 = 14.8 meter squared.

d) Volume of filtration material needed = 14.8 / 250 = 0.059 m3 = 59 liters. Introducing the safety factor of 1.5, we obtain a total of 1.5 x 59 = 89 liters of filtration material.
e) If the fish eat 225 grams per day equivalent to 2% of their body mass, it means we will have 225 grams / 0.02 = 11.25 kg of fish in our tank at full production levels.
f) Since we should not exceed 20 kg fish per cubic meter, we should have a fish tank that is at least 11.25 kg / (20 kg / m3) = 0.60 cubic meters large (or 600 L).

# Annex II: Interesting Aquaponics links

a. A comprehensive document by the FAO (2014) on small-scale & low-cost aquaponic systems. Everything you need to know to design and care for home-grade systems. Building instructions included.
http://www.fao.org/3/a-i4021e.pdf
b. Iowa state university “how to do it yourself” 1 hour webinar (with US aquaculture association).
http://www.ncrac.org/video/aquaponics-how-do-it-yourself
c. Aquaponics resource compilation (pdf and videos) by US department of Agriculture. https://www.nal.usda.gov/afsic/aquaponics
d. Aquaponics—Integrating Fish and Plant Culture, James Rakocy. Important facts and design figures.
http://pods.dasnr.okstate.edu/docushare/dsweb/Get/Document-10215/SRAC-454web.pdf
e. Comprehensive youtube video series by Bright Agrotech LLC. https://www.youtube.com/user/BrightAgrotechLLC/playlists
f. Aquapioneers kit design files & youtube video series on on how to care for the Aquapioneers kit.
http://aquapioneers.io/community-forum/

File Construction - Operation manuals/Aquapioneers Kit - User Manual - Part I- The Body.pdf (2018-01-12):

# Download kit

## Free documentation & blueprints for Aquapioneers Kit v1.6 Part I - Wooden structure - The Body

### VISIT: www.aquapioneers.io

### FOLLOW: @aquapioneers (Twitter / Instagram / Youtube)

### COMMENT: http://aquapioneers.io/community-forum/

### LIKE: https://www.facebook.com/aquapioneers/

### MAKE: https://github.com/aquapioneers/Aquapioneers-Kit-Barcelona-Design

# AQUAPIONEERS KIT MAIN FEATURES

The Aquapioneers Ecosystem is a thoughtfully crafted fun,
educational, | and | rewarding
experience.

At the intersection of hardware and ecology, it allows you to grow fresh and tasty food all year round. This little piece of nature, will engage and inspire you, your family and your
friends.

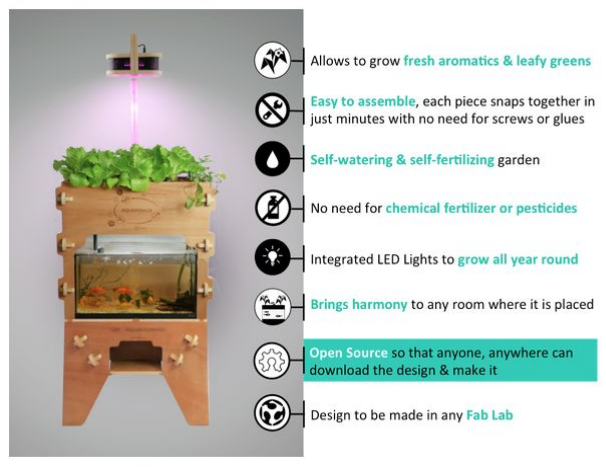
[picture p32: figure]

You can watch the following 30s timelapse Youtube video (https://www.youtube.com/watch?v=1fn3PVXYJCE) that sum up the overall assembly process and show a one month growing period with lettuces.

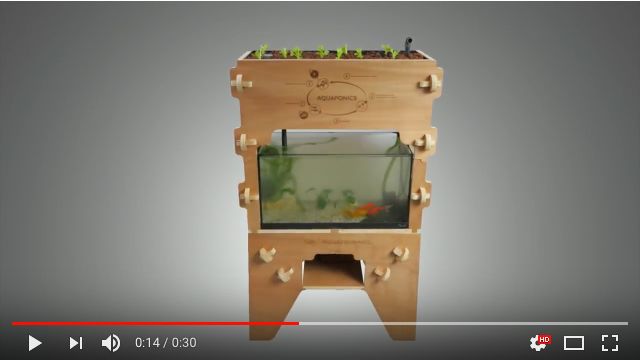
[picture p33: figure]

Please note that the blueprints for Aquapioneers Kit v1.6 have been designed for a specific aquarium dimension (60x30x30cm) which is the most common in Europe. Please make sure you can find these dimensions in your area before you proceed. If you can not source an aquarium with these dimensions, you will have to modify the structure design to be compatible.

# SOME HERBS & LEAFY GREENS YOU CAN GROW

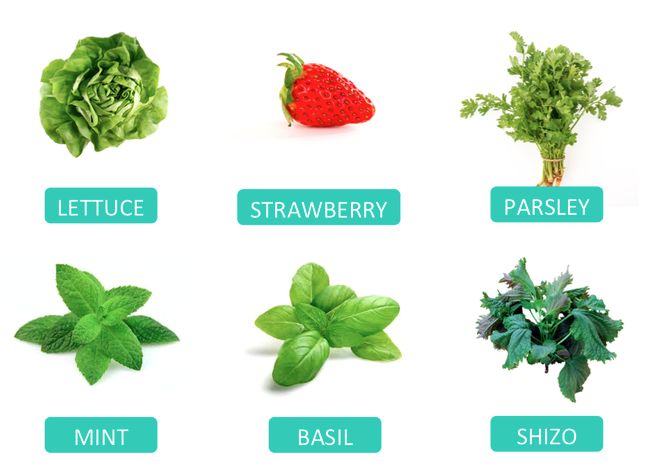
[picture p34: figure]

# SOME SPECIES OF FISH THAT CAN INHABIT YOUR ECOSYSTEM

# Contents

Project Overview | 6
AQUAPIONEERS - What is this ? | 6
Open Source Non Commercial - Why ? | 6
Project toolkit | 8
Download-kit | 8
Forum | 8
Local Manufacturing | 8
Tutorials | 8
Project Goals | 9
AQUAPIONEERS ECOSYSTEM ANATOMY | 10
THE BODY | 12
BILL OF MATERIALS | 12
PROJECTION | 13
STEP 1: GETTING THE FILES | 14
Files Explained | 14
STEP 2: BRINGING IT TO YOUR CLOSEST MAKER SPACE | 15
PRICE EXPECTED | 15
CNC Milling | 16
STEP 3: GETTING THE WOODEN PARTS | 17
CUTTING LIST | 17
STEP 4: SANDING & WAXING THE WOODEN PARTS | 18
STEP 5: ASSEMBLY | 22
ASSEMBLY 1 : LEGS | 22
ASSEMBLY 2 : AQUARIUM LEVEL | 26
ASSEMBLY 3 : GROWBED | 28
Thanks to all our ULULE backers that made this project possible | 31

# Project Overview

# AQUAPIONEERS - What is this ?

AQUAPIONEERS is a Barcelona based social enterprise that aims to combine the unbeatable advantages of Aquaponics as a sustainable method of urban agriculture and the power of Digital Fabrication to unlock social innovation. Locally we develop creative services around aquaponics for schools, businesses and individuals and globally spread the word using open source tools.

The Aquapioneers Ecosystem is our first open source product. Its design and user manual documentation release has been possible thanks to our 248 backers that supported our crowdfunding on ULULE (https://www.ulule.com/aquapioneers/) closed on July 2017.

This document contains the information you will need to download, fabricate, assemble and use the Aquapioneers ecosystem v1.6 with confidence and grow aromatics all year round.

# Open Source Non Commercial - Why ?

The CC-BY-NC license we have chosen gives anyone the right to download, edit and remix their own versions of the AQUAPIONEERS ECOSYSTEM designs. We think participation in design is something to be actively encouraged. By adapting, improving and creating new variations of the ecosystem we hope to encourage research, innovation and a spirit of collaboration.

Because empowering people is one of the fundamental pillars of our project, we believe that everybody should have free access to this documentation to explore aquaponics and digital fabrication. Unfortunately in 2017 it is not yet possible to make a living out of free work.. this is why we have decided to limit the free use of our work to individuals. While we hope to inspire sustainable innovation with our work, we believe that economic value created from inventions should also benefit the inventors. This is why commercial use of this documentation will only be permitted through formal collaboration agreements. If you are interested in making commercial use of this work, please get in touch with us and we’ll do our best to find a way to work together!

You are free to | Under the following terms
SHARE — copy and redistribute the material in any medium or format | ATTRIBUTION— You must give appropriate credit, (https://creativecommons.org/licenses/by-nc/3.0/#) provide a link to the license, and indicate if changes were made. (https://creativecommons.org/licenses/by-nc/3.0/#) You may do so in any reasonable manner, but not in any way that suggests the licensor endorses you or your use.
ADAPT— remix, transform, and build upon the material | NON COMMERCIAL — You may not use the material for commercial purposes. (https://creativecommons.org/licenses/by-nc/3.0/#)
The licensor cannot revoke these freedoms as long as you follow the license terms. | No additional restrictions — You may not apply legal terms or t (https://creativecommons.org/licenses/by-nc/3.0/#)echnological measures (https://creativecommons.org/licenses/by-nc/3.0/#) that legally restrict others from doing anything the license permits.
More info about this licence | https://creativecommons.org/licenses/by-nc/3.0/

# Project toolkit

# Download-kit

## Free documentation & blueprints

Starting an aquaponic system can be tricky, because quality information is rare and scattered all over the web. By open sourcing our design and its user guide, we want to break down the barriers of entry by ensuring that you work with the same system as the entire community and benefit from our collective experience.

We use Github to host our designs and file repositories. It allows anyone access to download files, make changes, “fork” new versions and work in a distributed and networked fashion. If you’d like to contribute to the project, Github is the place to make
comments | and | add | your | work:
https://github.com/aquapioneers/Aquapioneers-Kit-Barcelona-Design (https://github.com/aquapioneers/Aquapioneers-Kit-Barcelona-Design)

# Forum

### A place to meet & help each other

If we don’t share what we know, how can we learn from each other? We would like to encourage all participants to contribute what they can to improve the project. This might be peer review, debugging existing designs, creating entirely new design, sharing tips to grow amazing vegs, and collectively study the mystery of aquaponics.

This forum is a place to share pictures, skills, knowledge and interests through ongoing conversation:
http://aquapioneers.io/community-forum/

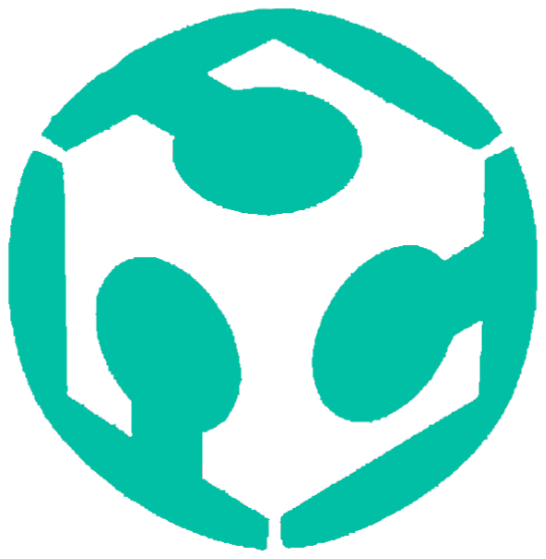
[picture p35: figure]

# Local Manufacturing

## +1200 maker spaces to build your kit

Check out these links to locate one in your city: www.themakermap.com. The Fablabs network: www.fablabs.io and also www.fabhub.io

# Tutorials

## Video tutorials to become an aquaponics

## hero

This new development will come along in 2018.

# Project Goals

1 Developing open source aquaponics designs that are suitable for local | and digital manufacturing and that can be optimised for locality.
| ● Developing a number of aquaponics designs that are used as a base for adaptation.
2 Creating a public library of aquaponic recipes through innovative forms | of citizen science.

### - Imagine a public library of aquaponic recipes, where each recipe is associated to a particular plant and tells you how to set your

ecosystem (i.e. fish density, lighting and environmental conditions,

etc) to suit this plant's needs. Just like a cooking book! - Together we are smarter! This library will be collaborative, meaning that each user will be encouraged to share his cultivation experience with the community. This way we can use our collective intelligence to figure out the best aquaponic recipes for each plant. The more the community participates, the better the recipes will be!

- Develop protocols and pathways for ‘Citizen Science’.
3 Bridging the information gap between aquaponics enthusiasts and | maker communities
| ● Encouraging information sharing between people with differing backgrounds and expertise. ● Developing a range of communication tools (forum, tutorials, download kit, tutorials) to facilitate innovation in local aquaponic farming.

# AQUAPIONEERS ECOSYSTEM ANATOMY

### The user manual has been divided into four blocks following the Aquapioneers Ecosystem

anatomy to ease its construction, assembly and use.

The release of this documentation is progressive, meaning that the first release will cover “The Body”. The following parts will be published during the weeks following the first edition,

### and will be regularly updated as a whole to reflect the comments and questions of our community. We thus encourage you warmly to leave any comments / suggestions /

### questions on our forum (http://aquapioneers.io/community-forum/) to be part of our

### community-based continuous improvement!

To give you a rough idea of how much it will cost you to make your kit, here is a table (based on material prices in Spain).

Item | Quantity | Cost | Total
Standard size wood board of 1220mm x 2440mm or 4 x 8 feet. | 1 | 48€ - 109€ depending on the type of plywood, pine being the cheapest | 48€ - 109€
CNC Milling See next section | 1,5 h Time needed to cut the pieces | 85€/h - 109€/h Based on professional use of Fab Lab machinery in Barcelona. This is highly dependent on the fab lab you will work with. In some cases it might be for free. | 0€ - 164€
Sanding & varnishing the two faces twice* | 6 m2 A standard size wood board represents 6m2 | 20€/m2 You can easily do this yourself, 20€/m2 represents the cost of a professional doing it for you | 10€ - 145€
60 W LED grow light Our design adapts to the 60W LED light module made by BCNLED. A different type of lamp may require design modifications on the light support. | 1 | 120€ | 120€
Acrylic aquarium cover | 60 x 30 x 0.4 cm | | 8€
Piping & sealing | | | 16€
Electricity | | | 36€
Aquarium equipment | | | 79€
Accessories | | | 116€
TOTAL (incl. VAT) | | | 433€ - 793€

A detailed list of materials will follow as the relevant parts of the documentation will be released.

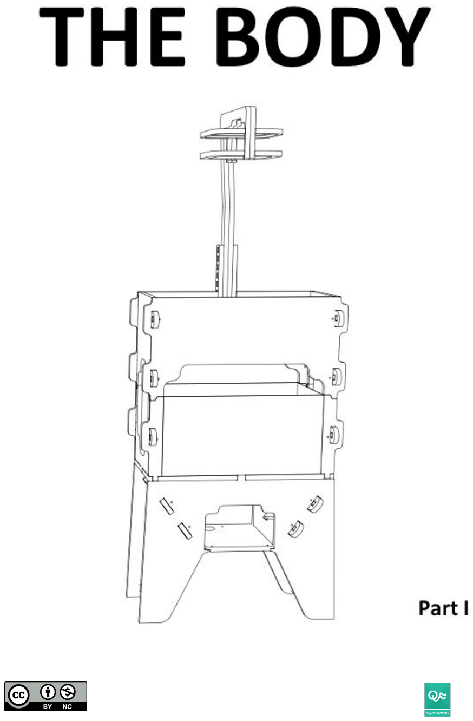
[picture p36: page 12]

# THE BODY

# BILL OF MATERIALS

## COMPONENTS

1. 2. 3. 4. 5. 6. | GROWBED BACK PANEL GROWBED FRONT PANEL LIGHT FRAME LIGHT LOCKS AQUARIUM BASE LEGS PLATE | x 1 x 1 x 2 x 3 x 1 x 1 | 7. 8. 9. 10. 11. 12. | WEDGES LIGHT SUPPORT PANELS AQUARIUM SIDE PANELS GROWBED PLATE GROWBED SIDE PANELS LEGS SUPPORT PANELS | x 20 x 2 x 2 x 1 x 2 x 2 | 13. 14. 15. 16. 17. | LIGHT SUPPORT BARS LEGS SIDE PANELS AQUARIUM FRONT PANELS BACK LEGS FRONT LEGS | x 2 x 2 x 4 x 1 x 1

Note : Numbers correspond to Cutting List (pg. 17)

# PROJECTION

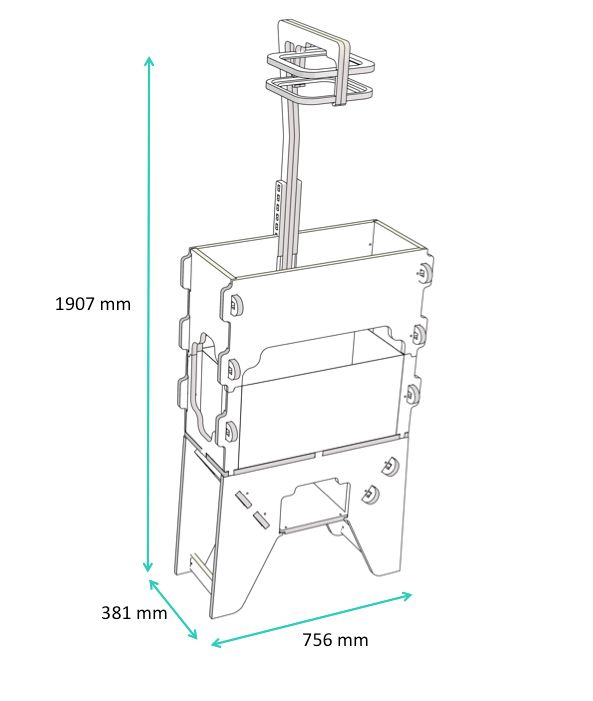
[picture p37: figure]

The Body is made of a wooden structure. This is the central piece that help you to turn a 54 L fish tank (600x300x300 mm) into an aquaponic ecosystem.

# STEP 1: GETTING THE FILES

## Files Explained

Source Files: https://github.com/aquapioneers/Aquapioneers-Kit-Barcelona-Design

AQUAPIONEERS KIT - v1.6 - 3D Model - 18mm.3dm Rhinoceros software has been used to generate this 3D model. Here you can play and tinker with the original designs.

AQUAPIONEERS KIT - v1.6 - Nesting - 18mm.3dm A nesting file is essentially a flat version of the design laid out to generate cutting strategies and tool paths. Adjust this file to calibrate it for different woods and machines.

# STEP 2: BRINGING IT TO YOUR CLOSEST MAKER SPACE

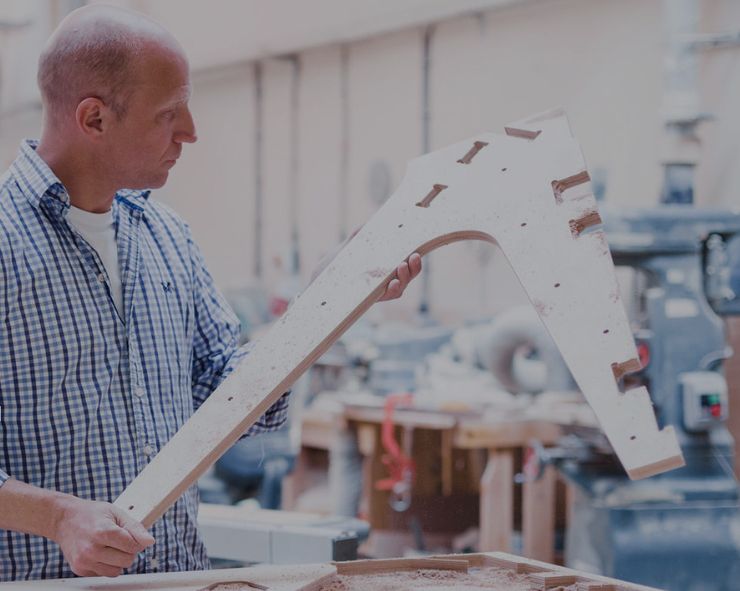
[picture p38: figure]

Check out these links to locate the closest Makerspace to your city:
- www.themakermap.com.
- The Fablabs network: www.fablabs.io
- and also www.fabhub.io

## PRICE EXPECTED

This section aims to give you price reference (without VTA) based on what a Barcelona based professional will charge you:

Item | Quantity | Price | Total
Standard size wood board of 1220mm x 2440mm or 4 x 8 feet. | 1 | 48€ - 109€ depending on the type of plywood, pine being the cheapest | 48€ - 109€
CNC Milling See next section | 1,5 h Time needed to cut the pieces | 85€/h - 109€/h Based on professional use of Fab Lab machinery in Barcelona. This is highly dependent on the fab lab you will work with. In some cases it might be for free. | 0€ - 164€
Sanding & varnishing the two faces twice* | 6 m2 A standard size wood board represents 6m2 | 20€/m2 You can easily do this yourself, 20€/m2 represents the cost of a professional doing it for you | 10€ - 145€
TOTAL (incl. VAT) | | | 58€ - 418€

* Please note that this budget can be easily drop down if you decide to do the sanding & varnishing by yourself (i.e. See Step 4 p. 18 for that).

## CNC Milling

CNC MILLING*

The Aquapioneers kits have been designed to be cut using one standard size wood board of 1220mm x 2440mm or 4 x 8 feet. This drawing shows the Geometry and Cut Strategies that a machine operator will need to use with their own CAM software. To help in the creation of the machine ‘tool paths’ we have split the strategies into colour coded layers and named them according to the strategy required. See the ‘Nesting’ and ‘Cut Strategy’ files.

CUT STRATEGIES

NOTE

We have created a file for 18mm thick boards. It is common for wood boards to have slight variations, so be careful to measure your wood before selecting the files. In this design every millimetre counts.

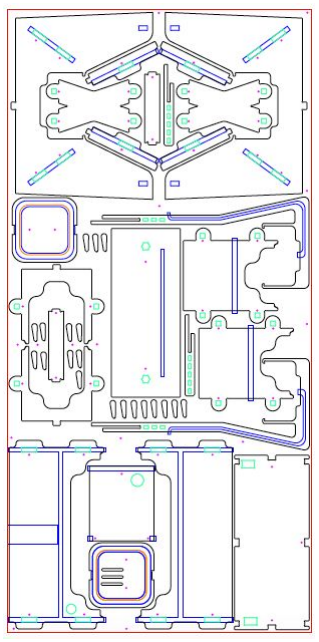
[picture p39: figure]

*A CNC router is a computer-controlled milling machine. They are often used to manufacture custom cabinetry and are available in most metropolitan areas. Check out these links to locate one in your city: www.themakermap.com. The Fablabs network: www.fablabs.io and also www.fabhub.io

# STEP 3: GETTING THE WOODEN PARTS

## CUTTING LIST

To facilitate the assembly (i.e. described in Step 5), we have named each part as described below

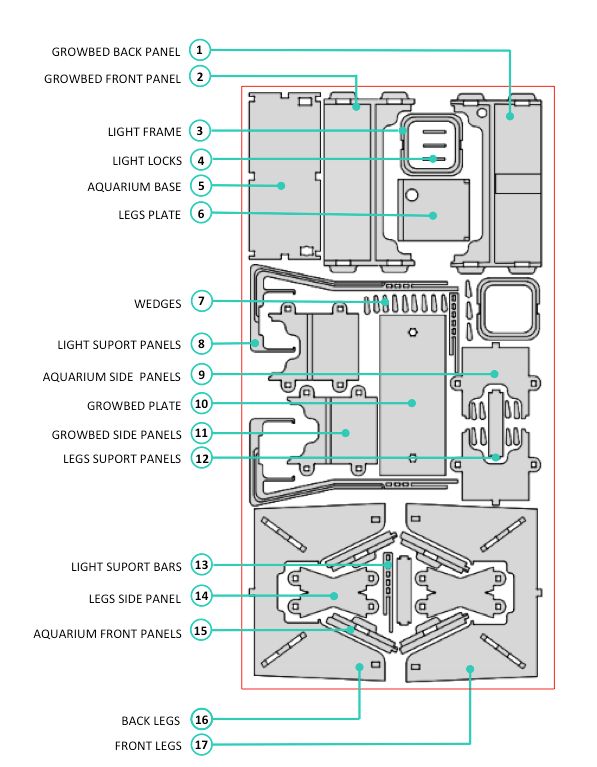
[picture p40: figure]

# STEP 4: SANDING & WAXING THE WOODEN PARTS

Once your wooden parts are cut, here come the fun part: sanding and varnishing / waxing. This will give you a color change and then it leave a protective coat on the surface of the wood against the humidity generated by the aquarium and growbed, as well as giving it a much better look!

Time expected | Expected cost
6 hours | 6€ for sanding paper 6€ for 750ml of Water based varnish 3,50€ for 250 ml furniture wax

For this you will need:

Electric sander Sanding paper disc 6 of 240 grit + 6 of 1200

Polishing Pads –
3000 grit to 5000
grit

500ml of Water
based varnish or
Finish wax

Roller brush

### Part by part, please follow the next steps:

# 1. SANDING

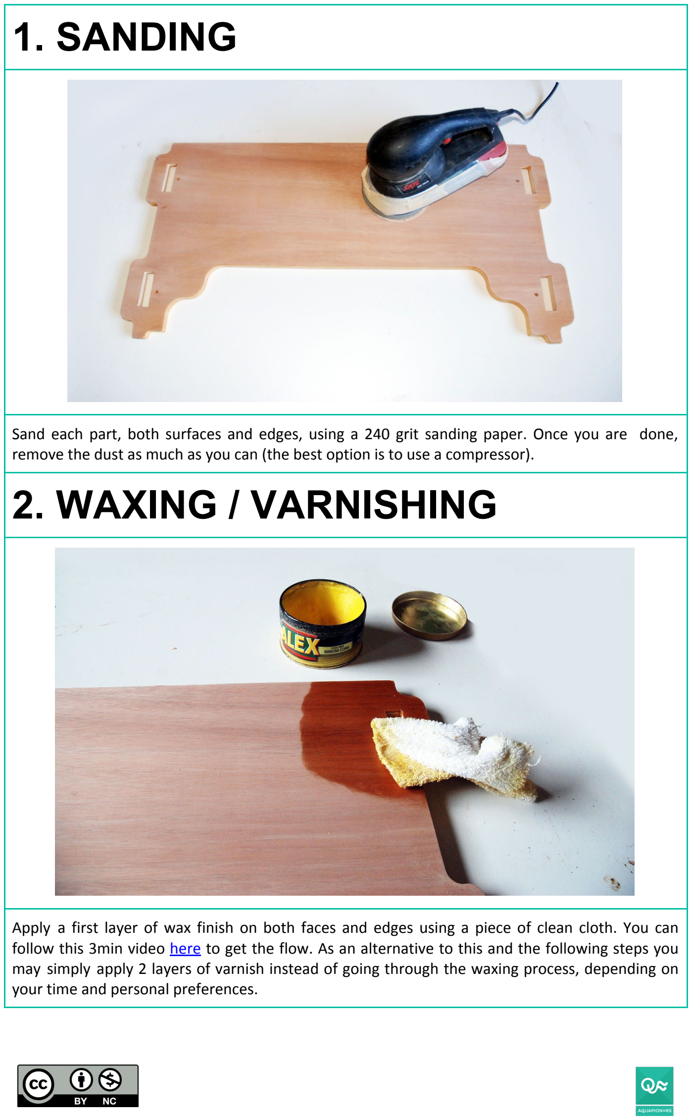
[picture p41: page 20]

Sand each part, both surfaces and edges, using a 240 grit sanding paper. Once you are done, remove the dust as much as you can (the best option is to use a compressor).

# 2. WAXING / VARNISHING

Apply a first layer of wax finish on both faces and edges using a piece of clean cloth. You can follow this 3min video here (https://www.youtube.com/watch?v=mPVQWMwVUzg) to get the flow. As an alternative to this and the following steps you may simply apply 2 layers of varnish instead of going through the waxing process, depending on your time and personal preferences.

# 3. FINE SANDING

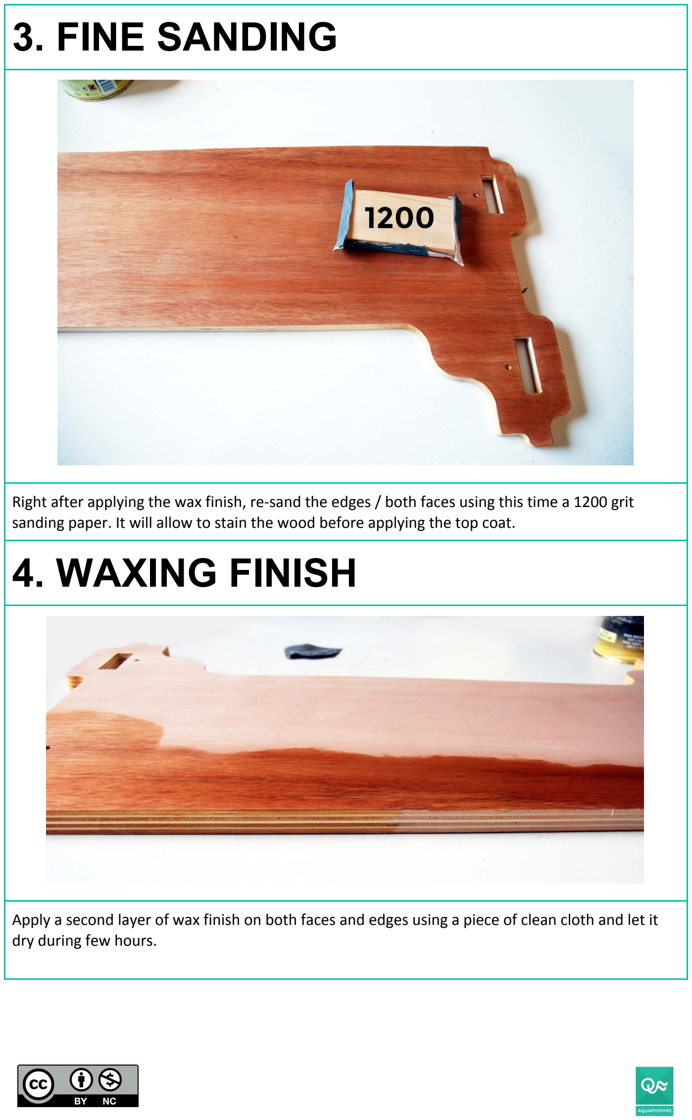
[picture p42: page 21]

Right after applying the wax finish, re-sand the edges / both faces using this time a 1200 grit sanding paper. It will allow to stain the wood before applying the top coat.

# 4. WAXING FINISH

Apply a second layer of wax finish on both faces and edges using a piece of clean cloth and let it dry during few hours.

# 5. POLISHING

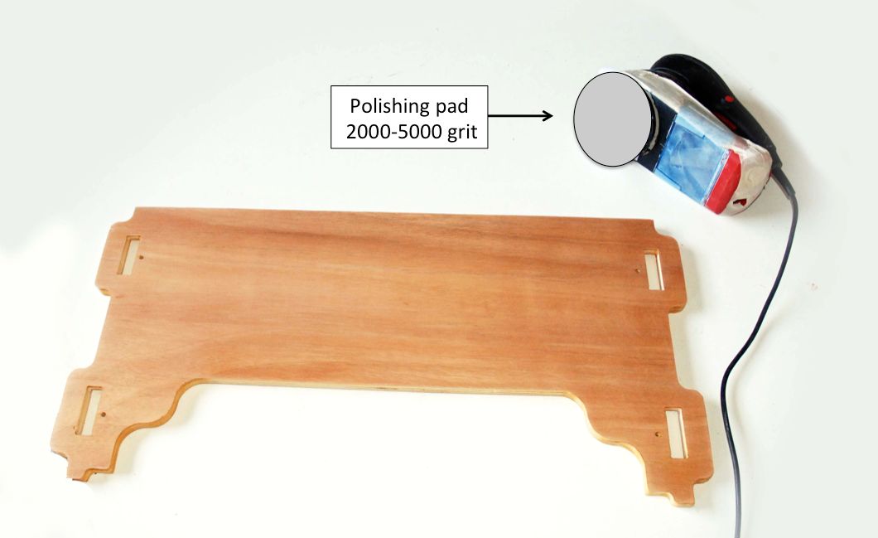
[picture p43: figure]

If you want a perfect finish you can go for polishing with finer abrasives. Here, the polishing system calls for dry, water-free products. Mount the polishing pad on your sander or polisher and set the speed to low and turn your machine on before touching down on the surface. Start your first pass at the left end, bottom corner and work your way to the right, keeping the machine moving at all times. When you get there, continue moving your machine to the next row, overlapping the first by approximately 50 percent, then work your way back to the left end.

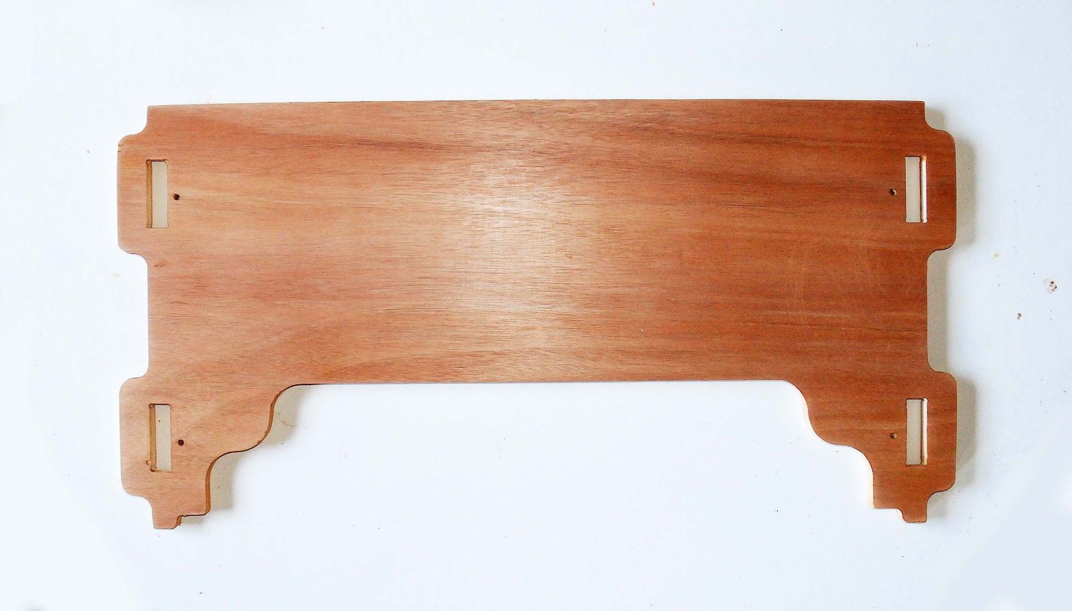
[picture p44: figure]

# STEP 5: ASSEMBLY

## ASSEMBLY 1 : LEGS

1

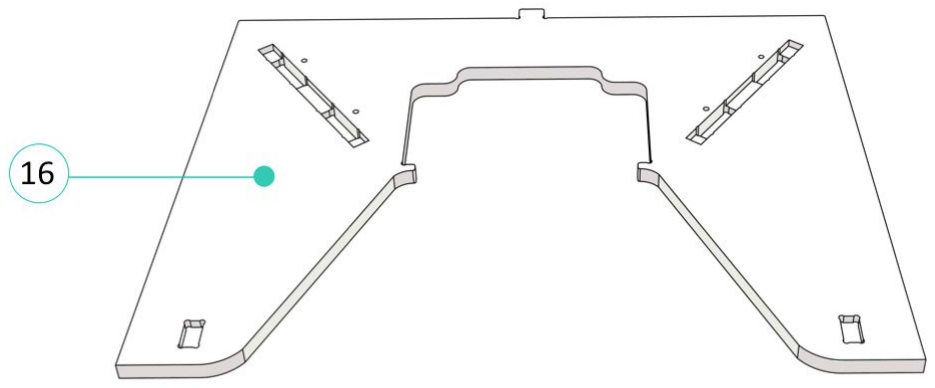
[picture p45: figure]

Lay the Back Legs on the floor and make sure the grooves are on the inside

Note: Protect your wood from damage by assembling your kit on a piece of cardboard or other protective material.
2

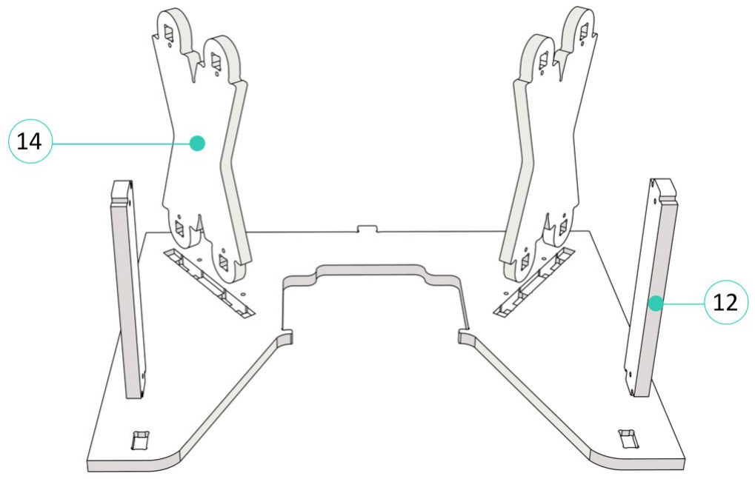
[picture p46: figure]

Place the two legs side panels and leg support panels into the corresponding slots.

3

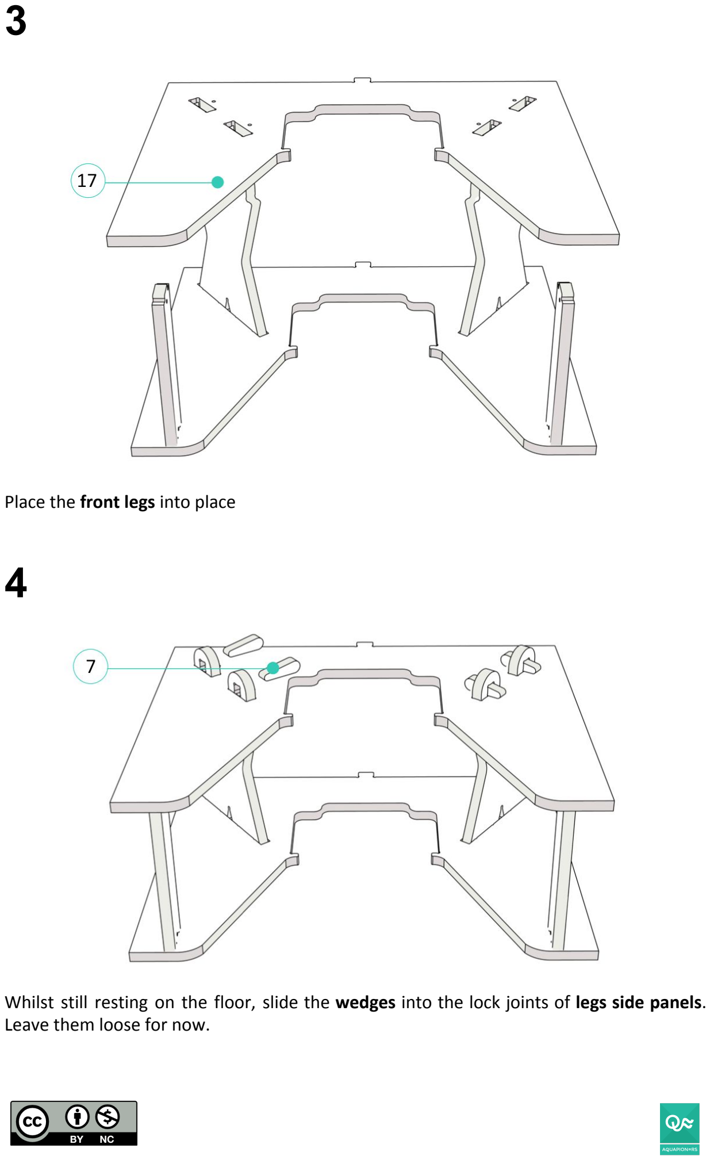
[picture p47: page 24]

Place the front legs into place
4

Whilst still resting on the floor, slide the wedges into the lock joints of legs side panels. Leave them loose for now.

5

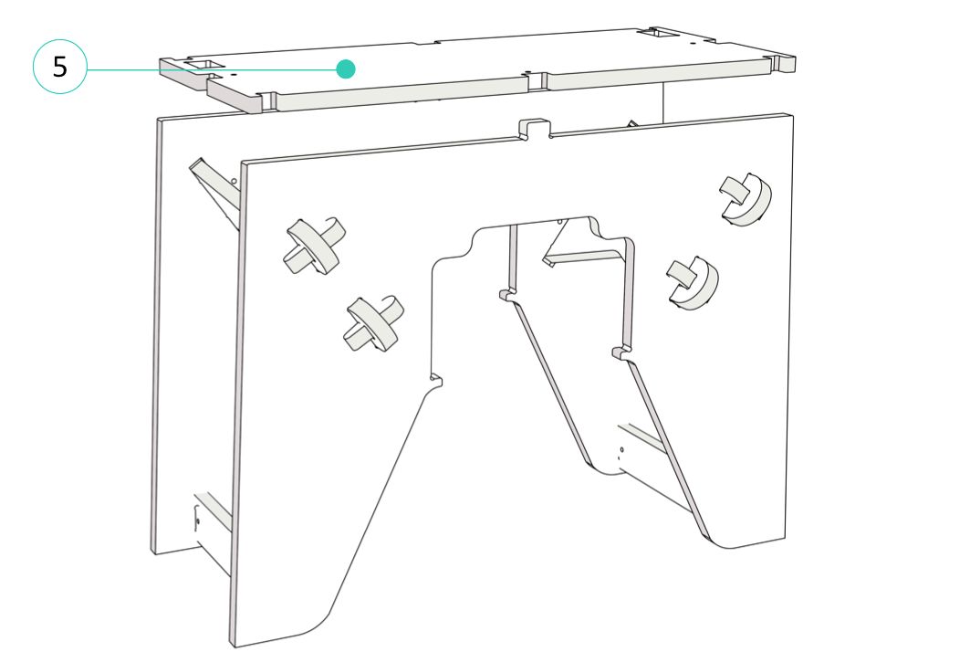
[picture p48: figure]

Place the aquaponics body in a vertical position and carefully place the aquarium base on top of the two legs making sure the two holes are facing backwards.
6

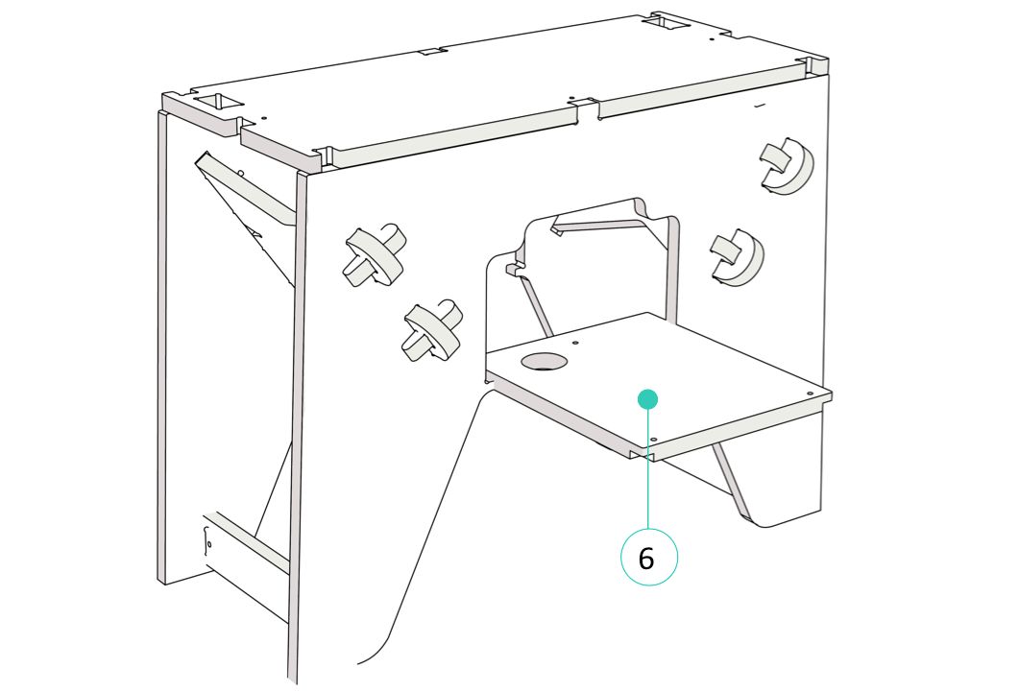
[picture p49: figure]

Push the legs plate in through the front entrance and slide it along the groves until it rests on the 4 slots of the leg panels.

7

### Legs part is done, let's get started with the aquarium level !

## ASSEMBLY 2 : AQUARIUM LEVEL

8


Add the aquarium side panels into the corresponding slots.
9


Make sure the handle cut into the side pieces are facing out.

Note: All rounded pieces should be at the top, while the square edges should beat the bottom to fit into the aquarium base. Pay close attention to the details in the diagram above.

10

Then slide the aquarium side panels carefully into the aquarium base.
11

Add the wedges to the lock joints of side panels. Leave them loose for now

Now, that we have the Legs assembled, we can focus on the “growbed”.

## ASSEMBLY 3 : GROWBED

12


Hold the growbed back panel upright. Then place the two growbed side panels into the corresponding slots. Make sure the grooves from all panels are on the inside.
13


Carefully push the growbed plate in through the front entrance and be sure that it slides along the groves and into the slot on the inside of the growbed back panel.

14


Whilst still resting on the floor add the wedges to the lock joints of front and back panels. Leave them loose for now.

We will focus on the “lighting system” later in the part IV “The nervous system”.


Once assembled, the wooden structure looks like this.

# Thanks to all our ULULE backers that made this project possible

### https://www.ulule.com/aquapioneers/

Dinis Mendes | Miren Garrido | &#39;Marco Sanalitro | Benny Krimeur | Pascale TEYSSIE
Miriam Hernandez | Thomas Jourdan | J Armand Figeac | Adriana Alvarez Caballero | Albert Siurana Saumell
Linda Sunnen | Kathleen Stewart | Anouk Le goueff | michaelboeckle3 | Marcio Barrios
ginnygin | Diana Moret | Gaby Xocolata | Mayo Fuster Morell | David Castillo Santander
Gabi Masfarre Pinto | Thiebault Mura | Romain Flattet | Felipe Agudelo Jaramillo | Visual Cabin
Marlene Clement | Glaucia Loebmann | Pierre Gachet | David Centeno | David Gomez Fontanills

Pablo Castellano | Anna Serena | Laurent Dussart | Jason Renoux | Fundacion Uxio Novoneyra
Lorenzi Nathalie | Mara Balestrini | Hong Park | Martine Neyen | Masanet Patrick
Anne Guimonnet | Aude Omerin | Isabel Wiseler-Lima | Mathieu Geiler | Goran Blazic
Helena Lahellen | Alexandre Benassar | Farrah Baut-Carlier | Albert Neyen | Vanessa Martnez
Pierre Tabary | Naoise Golden | Alexandre Curtelin | Kostia Belkin | Juan Manuel Umber rossello
Javier Verba | Roque Federico Dorfman | Gabriel Samso | Josh Edler | Robert Guia
Eva Miguelez Ortiz | Raf Sasan | Guillaume Teyssie | PATRICIA BASSE | Eileen Arnold
Patrice Boimond | Constance Dangy | Hugo Cabos | Charbel Aoun | julien bonnaud
Andrea Barbiero | AMPA La Sagrera AMPA La Sagrera | Olgui Fuertes | Mariana Quintero | Tania Sande
nith nith | Pierre Jean Nedergaard | Sergio Gutierrez | Alessio Verdolino | Walter D. Michaels
Anne Delacour | Anna Dalmases Trias | Yola Perez | Jose Francisco Pelaez | Jeanne Streng
CoworkingLille | Bruno Le Hen Ortega | Yola Perez | Muriel Chevallet | Oriol Cela
Alexia Mellor | Bruno Le Hen Ortega | Lydia Fraga | Roci,Silvia, Rocio SAN, Inigo,Guillem | Simon Burin des Roziers
Kevin Tang | Bruno Le Hen Ortega | Eduard Hernandez | Julia Cruz | Beryl Navarro
Yoshi Yasu Hirano | Marion Schuppe | Emilia Caba | Charles Labatut | Loic Fievet
ANDREW GREGSON | Josep Carrizo | Eva Del Barrio | Paul VERZY | Raquel Jimenez
Alberto Perez | Marie Tavera | Simon Malfiarge | Igor Garcia Barbero | Etienne Guyon
Elena Canas | noemie rousselet | Martin Gutmann | Agustin Vargas | Xavier Dominguez Aparicio
Daniel Carbonell Rubio | Isaac pierre racine | Katherine Woodhouse | Edmond Capart | lolilola50
Miren Garrido | Anna Garrofe | Fra Mousel | Bobby Marchand | Quentin Govignon
Guillaume & Loic | Gerard Chatelier | Justo Fab | Ivn Gutierrez | Francois DESORMEAU

Yasmine Abdelaziz | Gai Boro | Jaume Miro | Jean-Marie Guyon | acanigueral
Benjamin Whipker | Thomas Zannoni | Marie Scheid | Daniel Reznikov | Valentin Albinet
Michel Coqblin | Paul-Henri Petit | Dimitrios Savvopoulos | margaux tiberghien | Jean Christophe THUAN
Yee man annie Leung | Murielle Baugniet | Cales Laure | Cloud Coworking | Cecile Delacour Delhay
Julien Morey | PaCha | Tristan Copley Smith | Vicente Guallart | jordivallsfoix
Pierre Willieme | Constance Martel | Stef Denamps Gomez | Vicente Guallart | Ricardo Iglesias Meijome
Keith Anderle | Renee Teyssie | Laura Dayan | Joaquin Baraibar | Julius Brenn
jeremy Lizandier | Nicole Dorrell | marcel kellner | Emi_ouiwin | Anya Popova
Bea Nina Tartaruga | Pierre Paslier | Constance Dangy | Claudine Perla | philippa young
Matthieu Napoli | Arnau Arn | v25a | Adria Casas Gimeno | Martine Neyen
Harvey Dunham | Roger Delacour | Regis Decleire | Luciana Asinari | Maxime Le Goueff
clem sayyeah | Paul Deshayes | Breny Aceituno | Jesus Badenas | Martine Neyen
Amaya Pou | jean louis teyssie | Pierre-Francois Delacour | Guillaume Dardelin | Ivan Loza
Pauline Grenier | Johanne Greenwood | Mathieu PAUWELS | Maria Serrano Basterra | Guillaume & Loic
Andrea Ruani | Ana maria Gibert | Shai Erev Levi | Jean-marc Streng | Gerard Llorach
Jose Ivan Gonzalez Estrada | stephan le goueff | Gabriel Dulac-Arnold | Areti Markopoulou | javier baraibar molina
L.J. Eiben | simona-1 | samantha raez | Linda Carlson | Thomas GAUTHIER
marcin wolynski | Stephanie Ah Tchou | Antoine Desjonqueres | Silvia Brandi | Aude Omerin
Regis Largillier | Pascual Llanes | Corey Ellis | Lucas Cappelli | Jonathan Minchin
David Bertet | Angeles Ribes | Anahi Lacanna | Ana Vida | Alexandre Dubor
codeman | Tim Willemen | Charly Goerend | Gregoire Durrens | Helena Gibert
Adria Garcia I Mateu | Anaick Crozon | rieultecher | Naiara Chaler | Gaby Xocolata
Ricard Jornet | Caro Vignoli

### This Publication accompanies the Barcelona Aquapioneers ecosystem files and Assembly kit. It was designed and tested by the Aquapioneers team

at Valldaura Labs in Barcelona, Spain, with the generous support of Valldaura Labs, IAAC and Fab Lab Barcelona.

### CONTACT: info@aquapioneers.io

### VISIT: www.aquapioneers.io

### FOLLOW: @aquapioneers (Twitter/Instagram/Youtube/Linkedin)

### COMMENT: http://aquapioneers.io/community-forum/

### LIKE: https://www.facebook.com/aquapioneers/

### MAKE: https://github.com/aquapioneers/Aquapioneers-Kit-Barcelona-Design

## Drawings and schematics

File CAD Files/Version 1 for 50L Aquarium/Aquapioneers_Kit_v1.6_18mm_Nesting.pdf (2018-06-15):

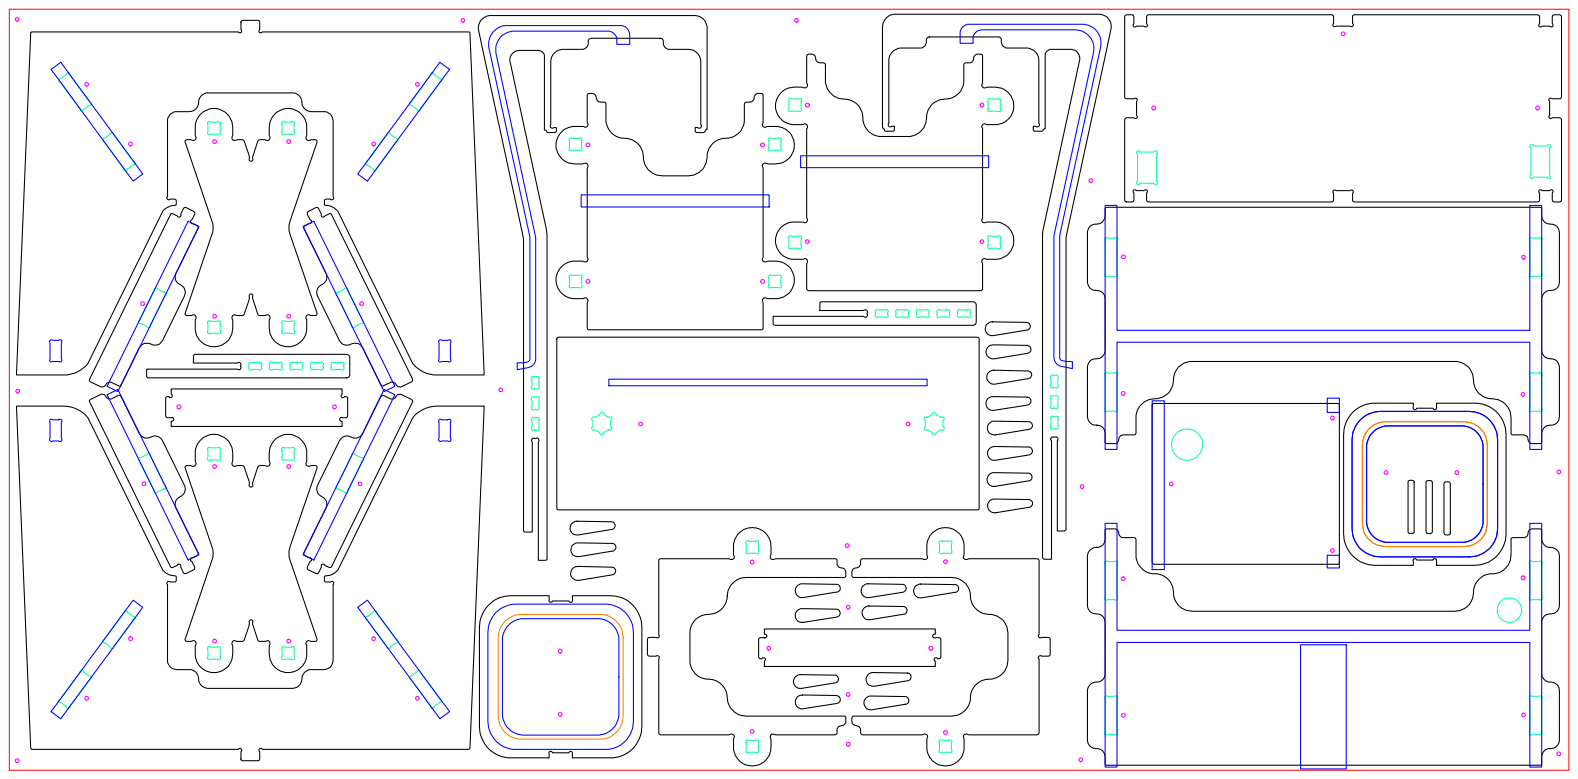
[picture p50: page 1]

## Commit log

2017-12-30 Create Assembly Manual
2018-01-12 added body documentation
    [Aquapioneers_Kit_v1.6_18mm_Nesting-2.3dm]
2018-10-25 Add Aquapioneers Kit - User Manual - Part III - The nervous system
    This documentation shows a step by step construction and assembly of the electrical system and monitoring system of the aquapioneers kit
2018-10-25 Create PCB layout
